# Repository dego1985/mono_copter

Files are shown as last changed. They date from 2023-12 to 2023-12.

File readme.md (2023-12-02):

## mono copter

* 自作モノコプターを作成した時のメモ。

## イメージ
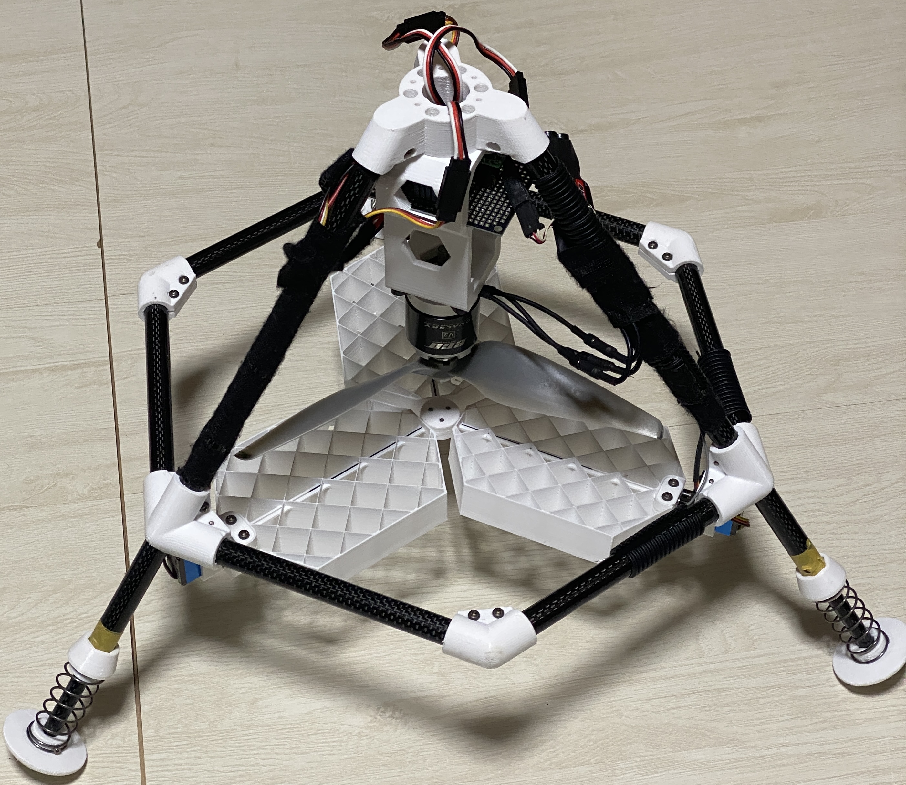
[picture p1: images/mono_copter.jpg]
mono copter

* 動画：
  * [フラフラ](https://youtu.be/5Qog1V-RosM)
  * [フラフラ2](https://youtu.be/LrC2EZjt1GY)
  * [墜落](https://youtu.be/phDMzeqYPqU)

## 材料

* raspberry pi pico 2040
  * 秋月：ＲＰ２０４０マイコンボードキット
  * Type-Cなのがお気に入り
* IMU
  * 秋月：ＢＭＸ０５５使用９軸センサーモジュール
  * 注意：センサーヒュージョンでクォータニオンまで計算してくれるモジュールもあります。
  * 今回は、自力で実装してみたかったので、生データ出力のみのモジュールを使った。
* プロポ（ヘリ用）・レシーバーセット(S.BUSプロトコル使用)
  * フタバ T10J
* カーボンパイプ
* リポバッテリー
  * 4セル
* モーター
  * デュアルスカイ ECO 2820C-V2 アウトランナーブラシレスモーター (800RPM/540W)
  * 最初は推力ギリギリのモーター使ってたけど、余裕のあるモーターの方が熱を持ちにくくてなんとなく良い気がする。
* ESC
  * HOBBYWING SKYWALKER 50A V2 ブラシレスESC
  * モーターへの大電流をコントロールするやつです
* サーボ(3個)
  * マイクロサーボ　ＭＧ９２Ｂ
  * メタルギアがいい感じ
  * それでも墜落した時に、負荷がかかりすぎて、ギアが割れて壊れた。
  * もう少し、馬力はなくても瞬発力がある方が良さそう。
* サーボケーブル延長
* プロペラ
  * [APC 9x8E 電動用３枚ペラ](https://www.little-bellanca.com/SHOP/21108.html)
  * プロペラの回転数や電流と推力の関係のデータシート
    * [公式パフォーマンスデータ](https://www.apcprop.com/technical-information/performance-data/)
    * 今回のプロペラは→PER3_9x8E-3.dat
* バネ
  * 足のバンパー用
* ねじ
  * とにかく軽くしたかったのでチタン製!
  * チタンB0ナベタッピング　M3X10
  * 他にも小さいねじを少々…

## 3D data

* パーツは、OpenSCADを使って設計し、3Dプリントしました
  * プログラミングみたいに設計できる！
* コード散らかってます…
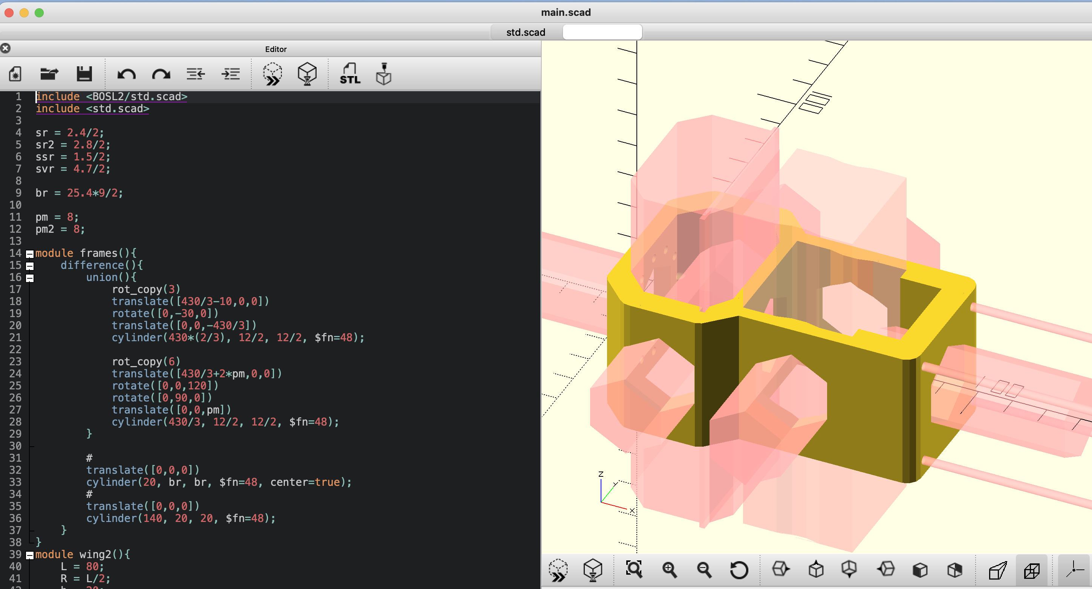
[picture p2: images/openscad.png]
openscad


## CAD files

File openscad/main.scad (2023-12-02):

include <BOSL2/std.scad>
include <std.scad>

sr = 2.4/2;
sr2 = 2.8/2;
ssr = 1.5/2;
svr = 4.7/2;

br = 25.4*9/2;

pm = 8;
pm2 = 8;

module frames(){
    difference(){
        union(){
            rot_copy(3)
            translate([430/3-10,0,0])
            rotate([0,-30,0])
            translate([0,0,-430/3])
            cylinder(430*(2/3), 12/2, 12/2, $fn=48);

            rot_copy(6)
            translate([430/3+2*pm,0,0])
            rotate([0,0,120])
            rotate([0,90,0])
            translate([0,0,pm])
            cylinder(430/3, 12/2, 12/2, $fn=48);
        }
        
        #
        translate([0,0,0])
        cylinder(20, br, br, $fn=48, center=true);
        #
        translate([0,0,0])
        cylinder(140, 20, 20, $fn=48);
    }
}
module wing2(){
    L = 80;
    R = L/2;
    h = 20;
    m = 0.5;
    h1 = 5;
    difference(){
        union(){
            hull(){
                mirror_copy([0,1,0])
                translate([20+R,10,-h+h1])
                cylinder(h, R, R, $fn=6);

                mirror_copy([0,1,0])
                translate([20+R-35,10,-h+h1])
                cylinder(h, R, R, $fn=6);
            }
        }
        translate([0,0,-m])
        hull(){
            mirror_copy([0,1,0])
            translate([100-5,svr+2+sr,0])
            cylinder(100, 5, 5, $fn=48);
            mirror_copy([0,1,0])
            translate([100,svr+2+sr,0])
            cylinder(100, 5, 5, $fn=48);
        }
        translate([90,0,0])
        rotate([0,90,0])
        cylinder(100, svr, svr, $fn=48);

        mirror_copy([0,1,0])
        translate([100-5,svr+2+sr,0])
        cylinder(100, sr, sr, $fn=48, center=true);
        rotate([0,90,0])
        cylinder(1000, 2.1/cos(30)/2, 2.1/cos(30)/2, $fn=6, center=true);
    }
    difference(){
        translate([100+7/2,0, -h+h1 +10/2])
        cube([7, 20, 10], center=true);
        rotate([0,90,0])
        cylinder(1000,  12.1/2*sqrt(2)+0.2, 12.1/2*sqrt(2)+0.2, $fn=48);
    }
}

module wing2_mask(){
    L = 80;
    R = L/2;
    h = 20;
    m = 0.5;
    difference(){
        union(){
            hull(){
                mirror_copy([0,1,0])
                translate([20+R,10,-20+5])
                cylinder(h, R, R, $fn=6);

                mirror_copy([0,1,0])
                translate([20+R-35,10,-20+5])
                cylinder(h, R, R, $fn=6);
            }
        }
        translate([0,0,-20])
        hull(){
            mirror_copy([0,1,0])
            translate([100-5,svr+2+sr,0])
            cylinder(100, 5, 5, $fn=48);
            mirror_copy([0,1,0])
            translate([100,svr+2+sr,0])
            cylinder(100, 5, 5, $fn=48);
        }
    }
}
module wing2_connector(){
    L = 80;
    R = L/2;
    h = 20;
    m = 0.5;
    difference(){
        translate([0,0,m])
        hull(){
            mirror_copy([0,1,0])
            translate([100-5,svr+2+sr,0])
            cylinder(5-m, 5, 5, $fn=48);
        }
        translate([90,0,0])
        rotate([0,90,0])
        cylinder(100, svr, svr, $fn=48);

        mirror_copy([0,1,0])
        translate([100-5,svr+2+sr,0])
        cylinder(100, sr, sr, $fn=48, center=true);
    }
}
module connector(){
    half_of([0,0,1], [0,0,-4])
    difference(){
        union(){
            mirror_copy([1,0,0])
            rotate([0,60,0])
            cylinder(pm+15, 12/2+4, 12/2+4, $fn=6);

            hull(){
                translate([0,0,-4])
                cylinder(5, 14, 14, $fn=48);

                hull(){
                    mirror_copy([1,0,0])
                    rotate([0,60,0])
                    translate([-12/2-4+5/cos(30),0,0])
                    cylinder(pm+15, 5/cos(30), 5/cos(30), $fn=6);
                }
            }
        }
        

        #
        hull()
        mirror_copy([1,0,0])
        rotate([0,60,0])
        translate([0,0,pm])
        cylinder(100, 0.3, 0.3, $fn=48);

        #mirror_copy([1,0,0])
        rotate([0,60,0])
        translate([0,0,pm])
        cylinder(100, 12/2, 12/2, $fn=48);
        
        #
        mirror_copy([1,0,0])
        rotate([0,60,0])
        translate([-12/2-sr-2,0,pm+15/2])
        rotate([90,0,0])
        {
            cylinder(100, sr, sr, $fn=48, center=true);
            mirror_copy([0,0,1])
            translate([0,0,5])
            cylinder(100, 3, 3, $fn=48);
        }
        
        rotate([0,0,90])
        rot_copy(2)
        {
            translate([12/2+3+2,0,0])
            {
                cylinder(100, sr,sr,$fn=48, center=true);
                translate([0,0,1])
                #cylinder(100, 3,3,$fn=48);
            }
        }
    }
}

module connector2(){
    difference(){
        union(){
            mirror_copy([1,0,0])
            rotate([0,60,0])
            cylinder(pm+15, 9, 9, $fn=48);

            sphere(9, $fn=48);
            hull(){
                mirror_copy([1,0,0])
                rotate([0,60,0])
                translate([-9/2,0, (pm+15)/2])
                cube([9, 10, pm+15], center=true);

            }
        }
        

        #
        hull()
        mirror_copy([1,0,0])
        rotate([0,60,0])
        translate([0,0,pm])
        cylinder(100, 0.3, 0.3, $fn=48);

        mirror_copy([1,0,0])
        rotate([0,60,0])
        translate([0,0,pm])
        cylinder(100, 12/2, 12/2, $fn=48);
        
        #
        mirror_copy([1,0,0])
        rotate([0,60,0])
        translate([-12/2-sr-2,0,pm+15/2])
        rotate([90,0,0])
        {
            cylinder(100, sr, sr, $fn=48, center=true);
            mirror_copy([0,0,1])
            translate([0,0,5])
            cylinder(100, 3, 3, $fn=48);
        }
        
    }
}
module connector3(){
    pitch = 50;
    h = 20;
    half_of([0,0,-1], [0,0,22])
    difference(){
        union(){
            mirror_copy([1,0,0])
            rotate([0,60,0])
            cylinder(pm+h, 9, 9, $fn=48);

            rotate([pitch,0,0])
            cylinder(pm2+h, 9, 9, $fn=48);

            sphere(9, $fn=48);

            hull(){
                mirror_copy([1,0,0])
                rotate([0,60,0])
                translate([-9/2,0, (pm+h)/2])
                cube([10, 10, pm+h], center=true);

            }
            half_of([0,-1,0])
            hull(){
                rotate([0,0,90])
                mirror_copy([1,0,0])
                rotate([0,pitch,0])
                translate([-10/2,0, (pm2+h)/2])
                cube([10, 10, pm2+h], center=true);

            }
        }
        

        
        hull()
        mirror_copy([1,0,0])
        rotate([0,60,0])
        translate([0,0,pm])
        cylinder(100, 0.3, 0.3, $fn=48);

        #
        hull()
        {
            rotate([0,0,-90])
            rotate([0,pitch,0])
            cylinder(100, 0.3, 0.3, $fn=48);
            translate([0,100,0])
            cylinder(100, 0.3, 0.3, $fn=48);
        }

        mirror_copy([1,0,0])
        rotate([0,60,0])
        translate([0,0,pm])
        cylinder(100, 12/2, 12/2, $fn=48);

        rotate([pitch,0,0])
        translate([0,0,pm2])
        cylinder(100, 12/2, 12/2, $fn=48, center=true);
        
        
        mirror_copy([1,0,0])
        rotate([0,60,0])
        translate([-12/2-sr-2,0,pm+h/2])
        rotate([90,0,0])
        {
            cylinder(11, sr, sr, $fn=48, center=true);
            mirror([0,0,1])
            translate([0,0,5])
            cylinder(100, 3, 3, $fn=48);
        }
        
        #
        rotate([0,0,-90])
        rotate([0,pitch,0])
        translate([-12/2-sr-2,0,pm2+h/2])
        rotate([90,0,0])
        {
            cylinder(11, sr, sr, $fn=48, center=true);
            mirror_copy([0,0,1])
            translate([0,0,5]){
                cylinder(5, 3, 3, $fn=48);
                cylinder(100, 2, 2, $fn=48);
            }
        }
    }
}

module connector4(){
    R=25;
    pitch = atan2(15,21);
    half_of([0,0,1], [0,0,-20])
    half_of([0,0,-1])
    difference(){
        union(){
            difference(){
                union(){
                    translate([0,0,-20])
                    cylinder(20, 20, 20, $fn=48);
                    
                    rot_copy(3)
                    half_of([0,0,1], [0,0,-20])
                    hull(){
                        translate([R,0,0])
                        rotate([0,-pitch,0])
                        translate([0,0,-20])
                        cylinder(60, 12/2+3, 12/2+3, $fn=48);

                        translate([0,0,-20])
                        cylinder(20, 12/2+3, 12/2+3, $fn=48);
                    }
                }
                cylinder(100, 10, 10, $fn=48, center=true);
            }
            rot_copy(3)
            translate([R,0,0])
            rotate([0,-pitch,0])
            translate([0,0,-25])
            cylinder(60, 12/2+3, 12/2+3, $fn=48);


            rot_copy(3)
            chain_hull(){
                translate([15,0,0])
                translate([0,0,-10])
                cylinder(10, 5,5,$fn=48);
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

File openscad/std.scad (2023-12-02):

include <BOSL2/std.scad>

module rot_copy(n){
    dtheta = 360/n;
    for(theta=[0:dtheta:359.99])
        rotate([0,0,theta])
        children();
}
module translate_(x,y,z){
    translate([x,y,z])
        children();
}
module rotate_(x,y,z){
    rotate([x,y,z])
        children();
}

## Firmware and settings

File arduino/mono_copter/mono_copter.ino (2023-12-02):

#include <Wire.h>
#include <Servo.h>
#include "receiver.h"
#include "servos.h"
#include "imu.h"
#include "pico/stdlib.h"

Receiver receiver;
Servos servos;
IMU_BMX055 imu;
const float radian_to_angle = 180 / PI;
void setup()
{

    Serial.begin(115200); // Terminal
    Serial.println("start setup");
    receiver.setup();
    Serial.println("start setup end");
}
void loop()
{
    bool updated = receiver.update();
    if (updated)
    {
        // receiver.print();
    }
}

void setup1()
{
    pinMode(16, OUTPUT);
    digitalWrite(16, LOW);
    delay(100);
    digitalWrite(16, HIGH);
    delay(100);

    // Wire(Arduino-I2C)の初期化
    Wire1.setSDA(6);
    Wire1.setSCL(7);
    Wire1.begin();
    Serial.println("start setup1");

    servos.setup();
    imu.setup();
    Serial.println("start setup1 end");
    delay(1000);
}
void get_steering(float &yaw, float &pitch, float &roll, int &throttle)
{
    const float beta = 1.0 / 600.0;
    yaw = -(receiver.get_channel(0) - 1030) * beta;
    pitch = (receiver.get_channel(1) - 1030) * beta;
    roll = -(receiver.get_channel(3) - 1030) * beta;
    throttle = receiver.get_channel(2);
}
int loop1_counter = 0;
float gx = 0;
float gy = 0;
float gz = 0;
void loop1()
{

    // get sensor
    imu.update();
    float gx0 = imu.imu.gyro.v.x;
    float gy0 = imu.imu.gyro.v.y;
    float gz0 = imu.imu.gyro.v.z;
    gx = 0.7 * gx + 0.3 * gx0;
    gy = 0.7 * gy + 0.3 * gy0;
    gz = 0.7 * gz + 0.3 * gz0;
    quat_t q = imu.q;
    quat_t v = imu.v;

    //  imu.print_quat_acc();
    //  imu.print_line();
    //  imu.print_gyro();
    //  imu.print_quat();

    // get receiver
    float yaw_rx, pitch_rx, roll_rx;
    int throttle;
    get_steering(yaw_rx, pitch_rx, roll_rx, throttle);

    // receiver.print();

    float yaw = 0;
    float pitch = 0;
    float roll = 0;
    // zero angular velocity
    float alpha = radian_to_angle * 0.5 / constrain(throttle / 1600.0, 0.1, 1);
    yaw = alpha * gz;
    pitch = alpha * gx;
    roll = alpha * gy;

    // zero velocity
    float alpha2 = radian_to_angle * 0.5 / constrain(throttle / 1600.0, 0.1, 1);
    yaw += 0;
    pitch = alpha2 * gx;
    roll = alpha2 * gy;

    // zero angle
    float gamma = radian_to_angle * 2.0 / constrain(throttle / 1600.0, 0.1, 1);
    yaw += gamma * q.v.z;
    pitch += gamma * q.v.x;
    roll += gamma * q.v.y;

    // receiver
    float lambda = radian_to_angle * 1.0 / constrain(throttle / 1600.0, 0.1, 1);
    yaw += lambda * yaw_rx;
    pitch -= lambda * pitch_rx;
    roll -= lambda * roll_rx;

    float angle_max = 40;
    const float angle1_0 = -5;  // right
    const float angle2_0 = -10; // left
    const float angle3_0 = -0;  // foward
    const float angle4_0 = 0;

    float angle1 = angle1_0;
    float angle2 = angle2_0;
    float angle3 = angle3_0;

    angle1 += constrain(-yaw + pitch - 0.5 * roll, -angle_max, angle_max);
    angle2 += constrain(-yaw - pitch - 0.5 * roll, -angle_max, angle_max);
    angle3 += constrain(-yaw + roll, -angle_max, angle_max);

    float throttle1 = throttle;
    servos.update(throttle1, angle1, angle2, angle3);
}

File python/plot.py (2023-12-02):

import time
from typing import List
import numpy as np
import quaternion
from quaternion import quaternion as quat

import pyqtgraph as pg
import pyqtgraph.opengl as gl
from pyqtgraph.Qt import QtCore
import serial


PORT = "/dev/tty.usbmodem1101"

np.set_printoptions(precision=3)
e = np.eye(3)
eq = np.array(
    [
        quat(0, 1, 0, 0),
        quat(0, 0, 1, 0),
        quat(0, 0, 0, 1),
    ]
)


def setup_serial() -> serial.Serial:
    ser = serial.Serial()
    # ser.baudrate = 115200
    ser.baudrate = 2000000
    ser.timeout = None  # タイムアウトの時間
    ser.port = PORT

    try:
        ser.open()
        print("open " + PORT)
    except Exception as e:
        print("can't open " + PORT)
        print(e)
        quit()

    return ser


class Axes3D:
    def __init__(self, scale=1.0) -> None:
        self.scale = scale
        xs = np.eye(3)
        self.arrows = [
            gl.GLLinePlotItem(
                pos=np.array([[0, 0, 0], xs[i]]),
                color=(*xs[i], 1),
                width=18,
                antialias=True,
            )
            for i in range(3)
        ]

    def addItemTo(self, w: gl.GLViewWidget):
        for i in range(3):
            w.addItem(self.arrows[i])

    def set_quat(self, q: np.ndarray, x: np.ndarray = quat(0, 0, 0, 0)):
        eq2 = q * eq * q.conj()
        offset = np.array([x.x, x.y, x.z])
        for i in range(3):
            pos = np.array([[0, 0, 0], [eq2[i].x, eq2[i].y, eq2[i].z]])
            self.arrows[i].setData(pos=pos * self.scale + offset)


class Cube3D:
    def __init__(self, scale=1.0) -> None:
        self.scale = scale
        xs = np.eye(3)
        self.arrows = [
            gl.GLLinePlotItem(
                pos=np.array([[0, 0, 0], xs[i]]),
                color=(*xs[i], 1),
                width=9,
                antialias=True,
            )
            for i in range(3)
        ]

    def addItemTo(self, w: gl.GLViewWidget):
        for i in range(3):
            w.addItem(self.arrows[i])

    def set_quat(self, q: np.ndarray, x: np.ndarray = quat(0, 0, 0, 0)):
        eq2 = q * eq * q.conj()
        offset = np.array([x.x, x.y, x.z])
        for i in range(3):
            pos = np.array([[0, 0, 0], [eq2[i].x, eq2[i].y, eq2[i].z]])
            self.arrows[i].setData(pos=pos * self.scale + offset)


class Arrow3D:
    def __init__(self, color, scale=1) -> None:
        self.scale = scale
        self.arrow = gl.GLLinePlotItem(
            pos=np.array([[0, 0, 0], [1, 0, 0]]),
            color=color,
            width=5,
            antialias=True,
        )

    def addItemTo(self, w: gl.GLViewWidget):
        w.addItem(self.arrow)

    def set_quat(self, q: np.ndarray):
        self.arrow.setData(
            pos=np.array([[0, 0, 0], [q.x, q.y, q.z]]) * self.scale
        )


class Scatter3D:
    def __init__(self, color, scale=1, r=None) -> None:
        self.r = r
        self.scale = scale
        self.points: List[np.ndarray] = []
        self.center = np.zeros(3, np.float32)
        self.scatter = gl.GLScatterPlotItem(
            pos=[], color=color, size=0.1, pxMode=False
        )

    def addItemTo(self, w: gl.GLViewWidget):
        w.addItem(self.scatter)

    def set_quat(self, q: np.ndarray):
        # update point
        v = quaternion.as_vector_part(q)
        if len(self.points) == 0:
            self.points.append(v)
        else:
            prev_normalized = normalize(self.points[-1])
            curr_normalized = normalize(v)
            diff_angle = np.linalg.norm(curr_normalized - prev_normalized)
            if diff_angle > 0.1:
                self.points.append(v)
                print(self.points[-1])

        # update center
        mag_correct = np.array(self.points) - self.center[np.newaxis, :]
        rs = np.linalg.norm(mag_correct, axis=-1, keepdims=True)
        if self.r is None:
            r = np.mean(rs)
        else:
            r = self.r
        self.center += 0.01 * np.mean(
            (rs - r) * normalize(mag_correct), axis=0
        )
        self.scatter.setData(
            pos=(np.array(self.points) - self.center) * self.scale
        )

        # remove outlier
        self.points = [
            x for x, r1 in zip(self.points, rs) if abs(r1 - r) / r < 0.3
        ]


def normalize(v: np.ndarray):
    norm = np.linalg.norm(v, axis=-1, keepdims=True)
    return v / norm


scatter = False
mag_show = False
acc_show = True
v_show = True
raw_show = False
z_off = True


class myApp:
    def __init__(self) -> None:
        # serial
        self.ser = setup_serial()

        pg.mkQApp("serial arror")
        w = gl.GLViewWidget()
        w.show()
        w.setWindowTitle("Arrow")
        w.setCameraPosition(distance=1)

        # grid
        g = gl.GLGridItem()
        g.scale(0.1, 0.1, 0.1)
        w.addItem(g)

        # pose
        self.axes = Axes3D(scale=0.05)
        self.axes.addItemTo(w)

        if acc_show:
            if raw_show:
                # acc raw arrow
                self.acc_raw_arrow = Arrow3D([1, 1, 1, 0.5], scale=0.01)
                self.acc_raw_arrow.addItemTo(w)

            # acc arrow
            self.acc_arrow = Arrow3D([1, 1, 1, 1], scale=0.01)
            self.acc_arrow.addItemTo(w)

        if v_show:
            # acc arrow
            self.v_arrow = Arrow3D([1, 0, 1, 1], scale=0.05)
            self.v_arrow.addItemTo(w)

        if mag_show:
            if raw_show:
                # mag raw arrow
                self.mag_raw_arrow = Arrow3D([1, 0, 1, 0.5], scale=0.001)
                self.mag_raw_arrow.addItemTo(w)

            # mag arrow
            self.mag_arrow = Arrow3D([1, 0, 1, 1], scale=0.001)
            self.mag_arrow.addItemTo(w)

        # time counter
        self.prev_time = time.perf_counter()

        if scatter:
            # mag scatter
            self.mag_scatter = Scatter3D(
                color=(1, 0, 1, 0.3), scale=0.01, r=120
            )
            self.mag_scatter.addItemTo(w)

            # acc scatter
            self.acc_scatter = Scatter3D(
                color=(1, 1, 1, 0.3), scale=0.1, r=9.80
            )
            self.acc_scatter.addItemTo(w)

        self.acc_ma = quat()

    def update(self):
        # read serial
        line = self.ser.readline().decode("utf-8").split(",")
        if len(line) != 1 + 3 * 3 + 3 * 3 + 4 + 3 * 3 or line[0] != "s":
            return
        self.ser.flushInput()
        line = line[1:]
        array = np.array(line).astype(np.float32).tolist()

        i = 0
        acc_raw = np.quaternion(0, *array[i : (i := i + 3)])
        gyro_raw = np.quaternion(0, *array[i : (i := i + 3)])
        mag_raw = np.quaternion(0, *array[i : (i := i + 3)])

        acc = np.quaternion(0, *array[i : (i := i + 3)])
        gyro = np.quaternion(0, *array[i : (i := i + 3)])
        mag = np.quaternion(0, *array[i : (i := i + 3)])
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

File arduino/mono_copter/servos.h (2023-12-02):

class Servos{
  const int MAX_SIGNAL = 1850;
  const int MIN_SIGNAL = 380;
  const int NEUTRAL_SIGNAL = (1700 + 380) / 2 - 100;
  Servo myservo[6];
public:
  Servos(){
  }
  void setup(){
    Serial.println("servos: setup start");
    
    myservo[0].attach(10);
    myservo[1].attach(11);
    myservo[2].attach(12);
    myservo[3].attach(13);
    myservo[4].attach(14);
    myservo[5].attach(15);

    Serial.println("servos: Writing maximum output.");
    myservo[0].writeMicroseconds(MAX_SIGNAL);
    Serial.println("servos: Wait 2 seconds.");
    delay(5000);
    Serial.println("servos: Writing minimum output");
    myservo[0].writeMicroseconds(MIN_SIGNAL);
    Serial.println("servos: Wait 2 seconds. Then motor starts");
    delay(5000);
  
    Serial.println("set servos 1,2,3 to 90 degree ");
    myservo[1].write(90);
    myservo[2].write(90);
    myservo[3].write(90);

    Serial.println("servos: setup end");

  }
  void update(float throttle1, float angle1, float angle2, float angle3){
    throttle1 = NEUTRAL_SIGNAL + (throttle1 - MIN_SIGNAL) * 0.7;
    myservo[0].writeMicroseconds(throttle1);
    myservo[1].write(angle1 + 90);
    myservo[2].write(angle2 + 90);
    myservo[3].write(angle3 + 90);
  }
};

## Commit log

2023-12-02 add 3d data
    [main.scad, std.scad]
2023-12-02 add: arduino code
